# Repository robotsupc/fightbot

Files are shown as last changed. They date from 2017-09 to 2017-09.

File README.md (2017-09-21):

# Fightbot

Fightbot is a 3D printed Mario Kart clone for less than 10$

Built by [Robots UPC](http://www.robotsupc.com), the UPC's Robotics student association.

RobotsUPC Fightbot (https://youtu.be/2lzYGl3RAvY)

[Click here to watch the short clip](https://youtu.be/2lzYGl3RAvY)

### How it looks

Fully assembled:



Without electronics:



Programming the robot:



From the back:



# How it works
To communicate to the arduino, it sets up an AP, called "RobotsUPC Fightbot X", where X is {1,2,3,4}.
When a client connects, we use a captive portal like setup, which will capture any URL and redirect it to the arduino itself.
For example you can visit example.com and you will be shown the robot's page.
This page, instead of the usual login page, shows a joystick that allows you to control the robot.
Since ajax and the likes are way too slow, we use WebSockets to communicate to the Arduino, obtaining excellent latency results.

# Design decisions
The body is completely 3D printed. The parts include holders and adapters for all electronics.
To use the arduino wirelessly, we need to use batteries. 4AA batteries provide 6V when fully charged, so we need to 
step this down to the 5V the arduino needs. We use the LM2596 DC step down module for this.

To **control it wirelessly**, we need to use a WiFi-capable Arduino, or use a RC receiver module.
The easiest way to do this is using a ESP8266 based controller, which **includes WiFi**, so we use the D1 mini.

The D1 mini uses the HG7881 motor driver, because it cannot supply the required current itself.

# Requirements
Bill of materials:
* 1x [D1 mini Arduino](https://www.aliexpress.com/item/D1-mini-Mini-NodeMcu-4M-bytes-Lua-WIFI-Internet-of-Things-development-board-based-ESP8266-by/32635160765.html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)
* 1x [LM2596 buck down](https://www.aliexpress.com/item/15924-Free-shipping-DC-DC-Step-Down-Converter-Module-LM2596-DC-4-0-40-to-1/32354635261.html)
* 1x [HG7881 motor driver](https://www.aliexpress.com/item/5pcs-lot-HG7881-HG7881CP-two-road-motor-driven-motor-driver-module-for-arduino-2-channel-motor/1919127484.html)
* 4x AA batteries
* 1x 4AA battery holder
* Some jumper wires
* About 20 M3 screws & nuts

You'll allso need:
* Screwdriver
* Soldering iron
* A knife
* A 3D printer

# Building
Coming soon.

# Results
We have presented the robot at the university's expo, obtaining amazing interest from other students.

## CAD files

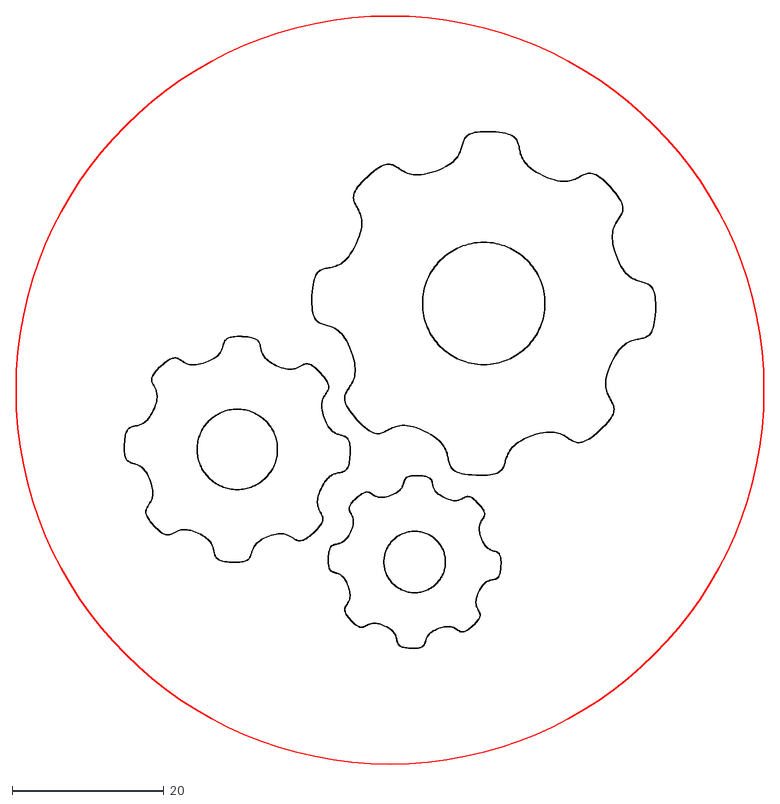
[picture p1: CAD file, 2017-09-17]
scad/logo.dxf
98.6 x 98.6

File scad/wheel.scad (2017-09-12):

$fn = 100;
module wheel(h) {
    difference() {
        cylinder(r=10, h=h);
        cylinder(r=3.3/2, h=h);
    }
}

wheel(5);

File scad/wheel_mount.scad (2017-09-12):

////    c1=costat llarg   c2=costat curt  h=alçada    g=gordura parets  d=distancia legs    w=distancia roda    ////

c1=65;
c2=28;
h=35;
g=3;
d=50;
w=10;

module s()
        cylinder(h=6.5,r=1.8,center=true,$fn=30);
    
module leg(){
    difference(){
        hull(){
            cylinder(h=g,r=5,center=true,$fn=30);
            translate([d,0,0])
                cylinder(h=g,r=5,center=true,$fn=30);
        }
        translate([d,0,0])
            cylinder(h=6.5,r=1.9,center=true,$fn=30);
    }
}
module sup(){
    rotate([0,90,0])
    rotate([90,0,0])
        leg();
    rotate([0,90,0])
    translate([0,w,0])
        rotate([90,0,0])
            leg();    
    translate([-5,-g/2,-1])
        cube([10,w+g,6]);
    translate([-17,w/2,g-1])
        hull(){
            cylinder(h=2*g,r=5,center=true,$fn=30);
            translate([17,0,0])
                cylinder(h=2*g,r=5,center=true,$fn=30);  
        }
    //translate([4,-0.5,-5])
        //cube([5,17,10]);
}

module wheel(){
    rotate([0,90,0])
        difference(){
            sup();
            translate([0,w/2,g-1])
                s();
            translate([-17,w/2,g-1])
                s();
            //translate([-5,g/2,0])
                //cube([13,w-g,2]);
        }
}

wheel();

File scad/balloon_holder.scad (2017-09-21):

th = 4;
glob_th = th;
screw_dst = 8.75;
screw_r = 3.5/2;

cone_r = 15;
cone_dst = 40;

module cone() {
    th = 2;
    gap_h = 15;
    h = 30;
    r=cone_r;
    pos = [-r,0,cone_dst-17];
    translate(pos)
    difference() {
        hull() {
            cylinder(r1=0, r2=r, h=h);
            //translate(-pos+[0,-((screw_r+th)*8)/2,cone_dst])
            //cube([0.0001,(screw_r+th)*8,13]);
            
            #translate(-pos) cube([th,(screw_r+glob_th)*2, 0.001], true);

        }
        
        translate([0,0,h/10+th])
        cylinder(r1=0, r2=r-th, h=h-th);
        
        translate([-18,0,0])
        cube([30,30,gap_h+th]*2, true);
        
        for (i = [0:3]) 
        translate([0,0,10-7*i]) rotate([0,90,0]) cylinder(r=screw_r, h=100, $fn=30);
        

    }
}

cone();

module holder() {
    cube_dst = screw_dst+11;
    translate([-cube_dst,0,0])
    difference() {
        hull() {
            cylinder(r=th+screw_r, h=th, $fn=30);
            translate([screw_dst,0,0]) cylinder(r=th+screw_r, h=th, $fn=30);
            translate([cube_dst,0,th/2]) cube([.00001,(screw_r+th)*2,th], true);
        }
        cylinder(r=screw_r, h=100, $fn=30);
        translate([screw_dst,0,0])cylinder(r=screw_r, h=100, $fn=30);
    }
    rotate([0,-45,0]) translate([0,0,6])    cube([6,(screw_r+th)*2, 3], true);
}

holder();

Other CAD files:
scad/battery_holder.scad
scad/d1mini_holder.scad
scad/lm2596_holder.scad
scad/logo.scad
scad/switch_holder.scad
scad/weapon_holder.scad

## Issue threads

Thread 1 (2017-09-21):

Image list

twinone, 2017-09-21:
Since GitHub doesn't support uploading images to README directly, we use an issue to upload the image to GitHub CDN and then link it in the README.

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

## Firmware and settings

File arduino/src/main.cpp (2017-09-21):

#include <Arduino.h>
#include <ESP8266WiFi.h>
#include <WebSocketsServer.h>
#include <ESP8266WebServer.h>
#include <DNSServer.h>

#include <Hash.h>
#include <robot3.h>


#define MOTOR_MIN_SPEED 768
#define MOTOR_MOVE_THRESHOLD 128

#define AIA D2
#define AIB D1
#define BIA D3
#define BIB D4

#define MOTOR_A 0
#define MOTOR_B 1




#define LED_PIN LED_BUILTIN

#define WEBAPP "<head><meta name='viewport'content='width=device-width,initial-scale=1'></head><style>body {width:100%;height:100%;margin:0px;}</style><canvas id='c'/><script>var b=document.getElementById('c'),c=b.getContext('2d'),d=0,e=0,g=0,h=0,k=0,l=0,m=0,n=0,p=0,q=!1,r=0,t,u=!1;b.addEventListener('mousedown',v,!1);b.addEventListener('touchstart',v,!1);b.addEventListener('mousemove',w,!1);b.addEventListener('touchmove',w,!1);b.addEventListener('mouseup',x,!1);b.addEventListener('touchend',x,!1);y();window.addEventListener('resize',z);z();t=new WebSocket('ws://192.168.4.1:81/');t.onopen=A;t.onerror=C;t.onmessage=D;y(); function A(){console.log('Connected to','ws://192.168.4.1:81/');u=!0;t.send('Hello from Client')}function D(a){console.log('MSG: ',a.data)}function C(a){u=!1;console.log('ERR',a)}function z(){b.width=window.innerWidth;b.height=window.innerHeight;g=b.width;h=b.height;m=b.width/2;n=b.height/2}function v(a){q=!0;void 0!=a.changedTouches&&a.preventDefault();w(a)} function w(a){q&&(void 0!=a.changedTouches&&a.preventDefault(),void 0!=a.changedTouches?(d=a.changedTouches[0].pageX,e=a.changedTouches[0].pageY):(d=a.x,e=a.y))}function x(a){void 0!=a.changedTouches&&a.preventDefault();q=!1} function y(){p=Math.min(g,h)/2*.7;var a=m-d;var f=n-e;a=Math.sqrt(a*a+f*f);a>p?(k=p/a*(d-g/2)+g/2,l=p/a*(e-h/2)+h/2):(k=d,l=e);q||(k=m,l=n);a=(new Date).getTime();100>a-r||(r=a,a=k-g/2,f=l-h/2,a=Math.floor(100*a/p),f=Math.floor(100*f/p),u&&t.send(a+' '+f));c.fillStyle='#E3F2FD';c.fillRect(0,0,g,h);c.strokeStyle='#7986CB';c.beginPath();c.moveTo(g/2,0);c.lineTo(g/2,h-1);c.stroke();c.beginPath();c.moveTo(0,h/2);c.lineTo(g-1,h/2);c.stroke();a=u?'#3F51B5':'#AAAAAA';E(.7,m,n,'#7986CB',!1);E(.3,k,l,a,!0); window.requestAnimationFrame(y)}function E(a,f,F,B,G){c.beginPath();c.arc(f,F,Math.min(g,h)/2*a,0,2*Math.PI);c.lineWidth=3;c.strokeStyle=B;c.fillStyle=B;G?c.fill():c.stroke()};</script>"

ESP8266WebServer server = ESP8266WebServer(80);
WebSocketsServer webSocket = WebSocketsServer(81);

IPAddress apIP(192, 168, 4, 1);
DNSServer dnsServer;

void moveMotor(int motor, int speed);




void blink(int t, int reps) {
  for (int i = 0; i < reps; i++) {
    digitalWrite(LED_PIN, HIGH);
    delay(t);
    digitalWrite(LED_PIN, LOW);
    delay(t);
  }
}

void processJoystick (int x, int y);

// https://stackoverflow.com/questions/29671455/how-to-split-a-string-using-a-specific-delimiter-in-arduino
String substr(String data, char separator, int index){
  int found = 0;
  int strIndex[] = {0, -1};
  int maxIndex = data.length()-1;

  for(int i=0; i<=maxIndex && found<=index; i++){
    if(data.charAt(i)==separator || i==maxIndex){
        found++;
        strIndex[0] = strIndex[1]+1;
        strIndex[1] = (i == maxIndex) ? i+1 : i;
    }
  }

  return found>index ? data.substring(strIndex[0], strIndex[1]) : "";
}

void webSocketEvent(uint8_t num, WStype_t type, uint8_t * payload, size_t length) {
    switch(type) {
    case WStype_DISCONNECTED:
        Serial.printf("[%u] Disconnected!\n", num);
        break;
    case WStype_CONNECTED: {
        IPAddress ip = webSocket.remoteIP(num);
        Serial.printf("[%u] Connected from %d.%d.%d.%d url: %s\n", num, ip[0], ip[1], ip[2], ip[3], payload);

        // send message to client
        webSocket.sendTXT(num, "Hello from Server");
        break;
    }
    case WStype_TEXT:
        //Serial.printf("MSG: %s\n", payload);
        String s = (char*) payload;
        int x = substr(s, ' ', 0).toInt();
        int y = substr(s, ' ', 1).toInt();
        processJoystick(x, y);
        break;
    }

}

void handleRoot() {
    server.send(200, "text/html", WEBAPP);
}

void setupWebServer() {
  server.on("/", handleRoot);
  server.on("/generate_204", handleRoot);
  server.on("/fwlink", handleRoot);
  server.onNotFound(handleRoot);
  server.begin();
}

void setupWSServer() {
  webSocket.begin();
  webSocket.onEvent(webSocketEvent);
}

void setupDNS() {
  dnsServer.setTTL(300);
  dnsServer.setErrorReplyCode(DNSReplyCode::ServerFailure);
  dnsServer.start(53, "*", apIP);
}

void setup() {
  pinMode(LED_PIN, OUTPUT);
  pinMode(AIA, OUTPUT);
  pinMode(AIB, OUTPUT);
  pinMode(BIA, OUTPUT);
  pinMode(BIB, OUTPUT);
  //digitalWrite(AIA, HIGH);
  //digitalWrite(AIB, LOW);


  setupDNS();

  blink(30, 10);

  Serial.begin(115200);
  Serial.println();
  Serial.println();
  Serial.println();

  Serial.print("Setting up WiFi soft-AP ... ");
  bool result = WiFi.softAP(SSID, PASS, CHAN, 0);
  if(result == true) Serial.println("Ready");
  else Serial.println("Failed!");

  setupWSServer();
  setupWebServer();

//  moveMotor(MOTOR_A, 100);
//  moveMotor(MOTOR_B, -100);
}

//formula distancia en plano cartesiano, siempre comparamos con el origen(0,0)
int distancefromCenter(int x, int y) {
  return sqrt((x*x)+(y*y));
}

void processJoystick(int x, int y) {
  //http://www.impulseadventure.com/elec/robot-differential-steering.html
  // Differential Steering Joystick Algorithm
  // Converts a single dual-axis joystick into a differential
  // drive motor control, with support for both drive, turn
  // and pivot operations.
  //

  // INPUTS
  int     nJoyX = x;              // Joystick X input                     (-128..+127)
  int     nJoyY = y;              // Joystick Y input                     (-128..+127)

  // OUTPUTS
  int     nMotMixL;           // Motor (left)  mixed output           (-128..+127)
  int     nMotMixR;           // Motor (right) mixed output           (-128..+127)

  // CONFIG
  // - fPivYLimt  : The threshold at which the pivot action starts
  //                This threshold is measured in units on the Y-axis
  //                away from the X-axis (Y=0). A greater value will assign
  //                more of the joystick's range to pivot actions.
  //                Allowable range: (0..+127)
  float fPivYLimit = 32.0;

  // TEMP VARIABLES
  float   nMotPremixL;    // Motor (left)  premixed output        (-128..+127)
  float   nMotPremixR;    // Motor (right) premixed output        (-128..+127)
  int     nPivSpeed;      // Pivot Speed                          (-128..+127)
  float   fPivScale;      // Balance scale b/w drive and pivot    (   0..1   )


  // Calculate Drive Turn output due to Joystick X input
  if (nJoyY >= 0) {
    // Forward
    nMotPremixL = (nJoyX>=0)? 99.0 : (99.0 + nJoyX);
    nMotPremixR = (nJoyX>=0)? (99.0 - nJoyX) : 99.0;
  } else {
    // Reverse
    nMotPremixL = (nJoyX>=0)? (99.0 - nJoyX) : 99.0;
    nMotPremixR = (nJoyX>=0)? 99.0 : (99.0 + nJoyX);
  }

  //  A PARTIR DE AQUI SE PUEDEN ELIMINAR COSAS, NO SON TAMPOCO LAS ENTIENDO
  //  AL 100%
  // Scale Drive output due to Joystick Y input (throttle)
  nMotPremixL = nMotPremixL * nJoyY/100.0;
  nMotPremixR = nMotPremixR * nJoyY/100.0;

  // Now calculate pivot amount
  // - Strength of pivot (nPivSpeed) based on Joystick X input
  // - Blending of pivot vs drive (fPivScale) based on Joystick Y input
  nPivSpeed = nJoyX;
  fPivScale = (abs(nJoyY)>fPivYLimit)? 0.0 : (1.0 - abs(nJoyY)/fPivYLimit);

  // Calculate final mix of Drive and Pivot
  nMotMixL = (1.0-fPivScale)*nMotPremixL + fPivScale*( nPivSpeed);
  nMotMixR = (1.0-fPivScale)*nMotPremixR + fPivScale*(-nPivSpeed);

  // Convert to Motor PWM range
  if (nMotMixL > MOTOR_MOVE_THRESHOLD)
    nMotMixL = map(nMotMixL, 0, 1023, MOTOR_MIN_SPEED, 1023);
  if (nMotMixR > MOTOR_MOVE_THRESHOLD)
    nMotMixR = map(nMotMixR, 0, 1023, MOTOR_MIN_SPEED, 1023);

  moveMotor(MOTOR_A, nMotMixL);
  moveMotor(MOTOR_B, nMotMixR);
}

void moveMotor(int motor, int speed) {
  //EL IA y el IB estan asignados de esta manera para que concuerde la
  //direccion con  rueda de atras y
  int low, pwm;
  if (motor) {
    low = AIB;
    pwm = AIA;
  }
  else {
    low = BIB;
    pwm = BIA;
  }
  if (speed < 0) {
    int tmp = low;
    low = pwm;
    pwm = tmp;
    speed = -speed;
  }


  int vel = map(speed, 0, 100, 0, 1023);

  Serial.print("VEL: ");
  Serial.println(vel);

  //digitalWrite(low, LOW);
  //digitalWrite(pwm, HIGH);
  analogWrite(low, 0);
  analogWrite(pwm, vel);
}

void loop() {
  //Serial.printf("Stations connected = %d\n", WiFi.softAPgetStationNum());
  dnsServer.processNextRequest();
  webSocket.loop();
  server.handleClient();
}

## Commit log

2017-09-05 Add arduino code to serve webapp
2017-09-05 Webapp sends normalized joystick data to Arduino
2017-09-07 Add battery holder
    [fightbot_battery_holder.scad]
2017-09-08 Add motor movement
2017-09-08 Placeholder motor function Arigato gozaimasu
2017-09-09 Add balloon holder
    [balloon_holder.scad]
2017-09-12 Add LM2596 holder
    [lm2596_holder.scad]
2017-09-12 Add wheel.scad
2017-09-12 Update battery holder
    [fightbot_battery_holder.scad]
2017-09-12 Add wheel, wheelmount battery holder, weapon holder
    [battery_holder.scad, weapon_holder.scad, wheel.scad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]
2017-09-13 Add d1mini_holder prototype
    [d1mini_holder.scad]
2017-09-13 Update d1mini holder
    [d1mini_holder.scad]
2017-09-13 Finalize ring vertex
    [ring_vertex.scad]
2017-09-14 Add switch holder prototype
    [switch_holder.scad]
2017-09-14 Update switch prototype
    [switch_holder.scad]
2017-09-14 Finalize switch holder
    [switch_holder.scad]
2017-09-17 Add logo
    [logo.dxf, logo.scad]
2017-09-21 Finalize balloon holder
    [balloon_holder.scad]
2017-09-21 Add logo and logo holder
    [logo.scad]
2017-09-21 Remove ring vertex
    [ring_vertex.scad]
